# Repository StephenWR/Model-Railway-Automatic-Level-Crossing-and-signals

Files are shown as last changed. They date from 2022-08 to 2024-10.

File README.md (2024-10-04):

# Model-Railway-Automatic-Level-Crossing-and-signals
Arduino based Automatic Level Crossing Gate Controller for double track line on a Model Railway (UK original style gates)
with CMRI reporting to JMRI

This project runs on an Arduino Nano with eight LDR-based sensors distributed along a double-track railway with the old style Level Crossing gates and a station at the centre.  The sensors detect a train entering the section from either side with at least 1 metre of track (n-gauge - more needed for OO or O gauge) to the level crossing gates - this allows time for the gates to close in sequence (exit gates last) to road traffic and open to Train traffic. The sensor for leaving the section is also >1metre away so that long trains will be clear of the gates before opening to road traffic.  Trains entering simultaneously on each track will not trigger the gates to open for road traffic until both have exited the section. Additionally, there is a two-aspect signal at the exit to the station which changes to green when the gates are open for train traffic and changes to red again immediately after being triggered by the train leaving the platform. All the sensor data is sent to a computer running JMRI using a CMRI USB connection - the serial.print lines are commented out when CMRI is running - and are active only when debugging the hardware.

Traffic is only permitted in one direction for each line so that the software is only triggered in the correct sequence—this reduces the chance of spurious triggering and "switch bounce."  Pins are now used for warning signals to road traffic — this is operating now after I designed some for 3D printing using a Resin printer.  Ironically, having spent time designing prototypical hoods for the traffic warning lights, I have had to remove the hoods to make it obvious that the lights are working because they were only viewable at the same height as the road, and most viewers are taller and don't see the lights flashing - i.e. the hoods worked too well!

The version uploaded 3rd October 2024 is used on Maun Valley Junction layout where the station stopping sensors are not used, hence only 6 sensors are used.

3D printing files are available at https://www.thingiverse.com/thing:6786859

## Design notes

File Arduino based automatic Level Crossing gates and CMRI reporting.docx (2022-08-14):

Arduino - based Automatic Level Crossing (on a budget!)

This small project describes an automatic level crossing system controlling 4 UK style Level Crossing Gates, 2 signals (one for the down track and one for the up track) using one “Arduino Nano” (< £9 including terminals) – and 8 LDR sensors in the track (~ 10p each) and 4 small servo motors (<£1 each). The 3D printed parts including the holding base and gates cost <£2.

Our layout has a lower level which is DCC controlled with twin tracks with a station in the middle and a level crossing next to it, and both tracks are fitted with two 3 aspect signals with sensors placed immediately after each signal. The other 2 sensors per track are placed just before and just after the fiddle yards for each circuit – see the simplified schematic below. The outer loop direction is clockwise, the inner loop anticlockwise.

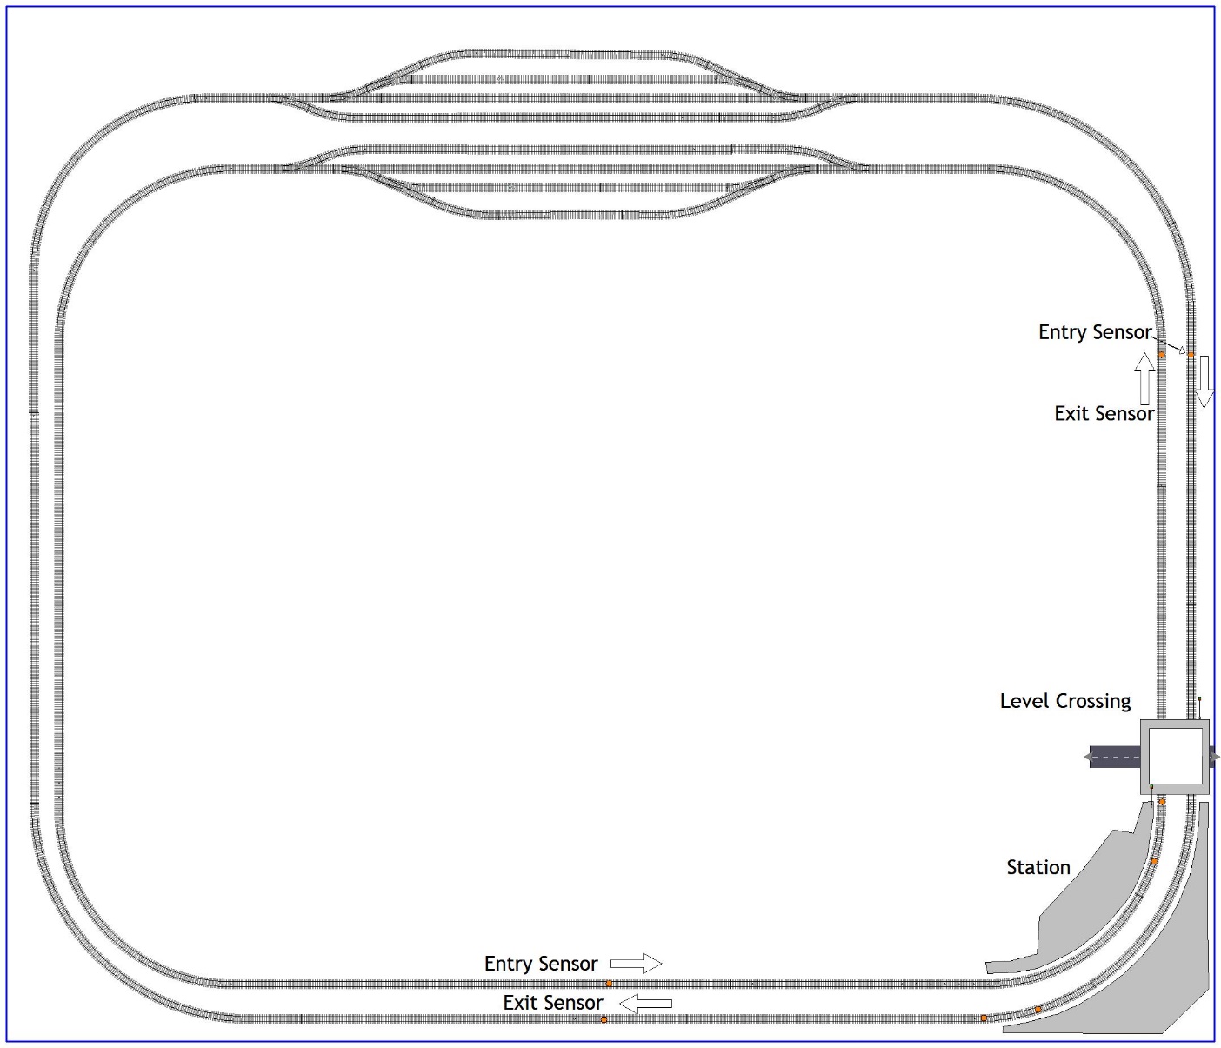
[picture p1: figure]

This project runs on an Arduino Nano with eight LDR based sensors distributed along a double track railway with the old style Level Crossing gates and a station at the centre. The sensors detect a train entering the section from either side with at least 1 metre of track (n-gauge - more needed for OO or O gauge) to the level crossing gates - this allows time for the servo controlled gates to close in sequence (exit gates last) to road traffic and open to Train traffic. The sensor for leaving the section is also >1metre away so that long trains will be clear of the gates before opening to road traffic. Trains entering simultaneously on each track will not trigger the gates to open for road traffic until both have exited the section. Additionally there is a two aspect signal at the exit to the station which changes to green when then the gates are open for train traffic and changes to red again immediately after being triggered by the train leaving the platform. All the sensor data is sent to a computer running JMRI using a CMRI USB connection - the serial.print lines are commented out when CMRI is running - and are active only when debugging the hardware.

Traffic is only permitted in one direction for each line, so that the software is only triggered in the correct sequence - this reduces the chance of spurious triggering and "switch bounce".

The gate mechanism is 3D printed comprising a base which holds 4 servo motors so that the spindles are vertical, a top plate to the base unit to hold in place the spindle extensions into which the Level Crossing Gates engage with a friction fit so that in the case of a train crashing into gates still closed to Trains, little damage will be caused. By default the gates are closed to Trains, and close to traffic in the sequence that moves the left gates first and the right gates last to enable cars on the crossing to exit without hitting the gates.

The Arduino sketch is shown at the GitHub repository under https://github.com/StephenWR/Model-Railway-Automatic-Level-Crossing-and-signals

}

The Arduino Nano with terminal block

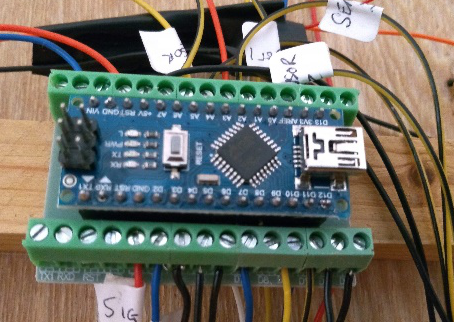
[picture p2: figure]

IR sensor module with 5mm Tx/Rx diodes.

(For n-gauge replace with 3mm diodes)

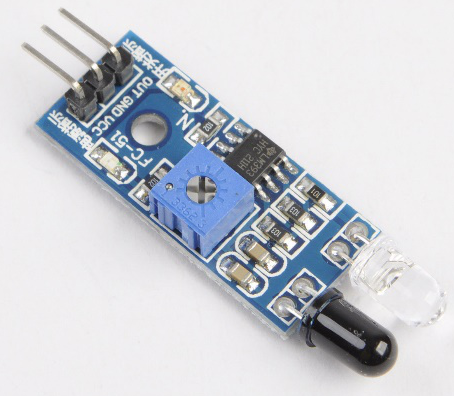
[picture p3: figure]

MERG Arduino Workshop 26Oct19.docx © Stephen Wadsworth 2019Page 1 of 3

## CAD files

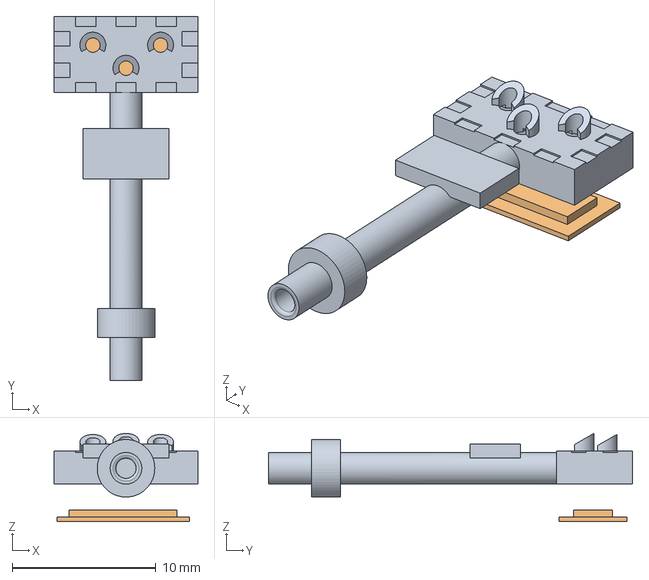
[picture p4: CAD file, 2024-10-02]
Level crossing warning lights 6.FCStd
10.0 x 25.3 x 6.12 mm

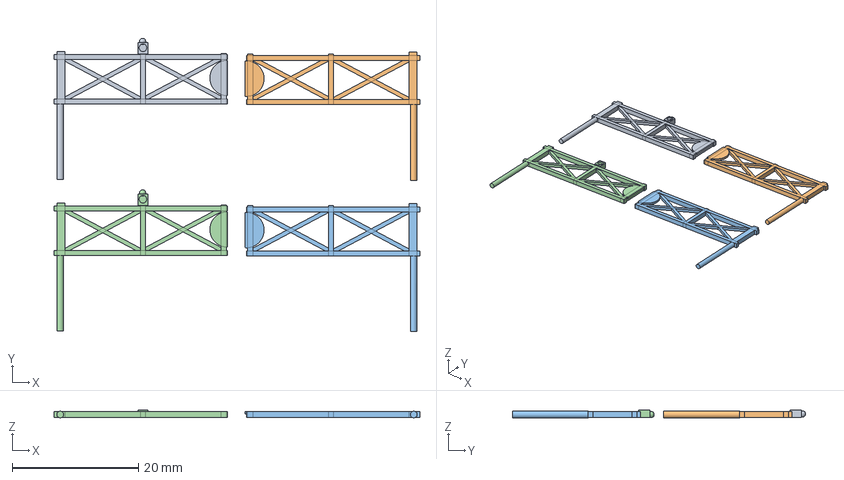
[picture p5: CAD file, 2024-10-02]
Level crossing gates v2 n gauge.FCStd
58.0 x 46.5 x 1.23 mm

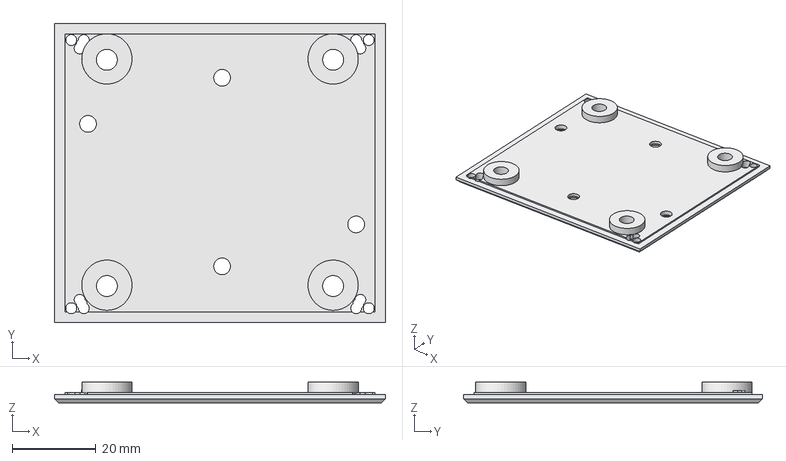
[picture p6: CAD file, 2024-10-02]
Level crossing top6 n gauge.FCStd
79.0 x 71.5 x 5.00 mm

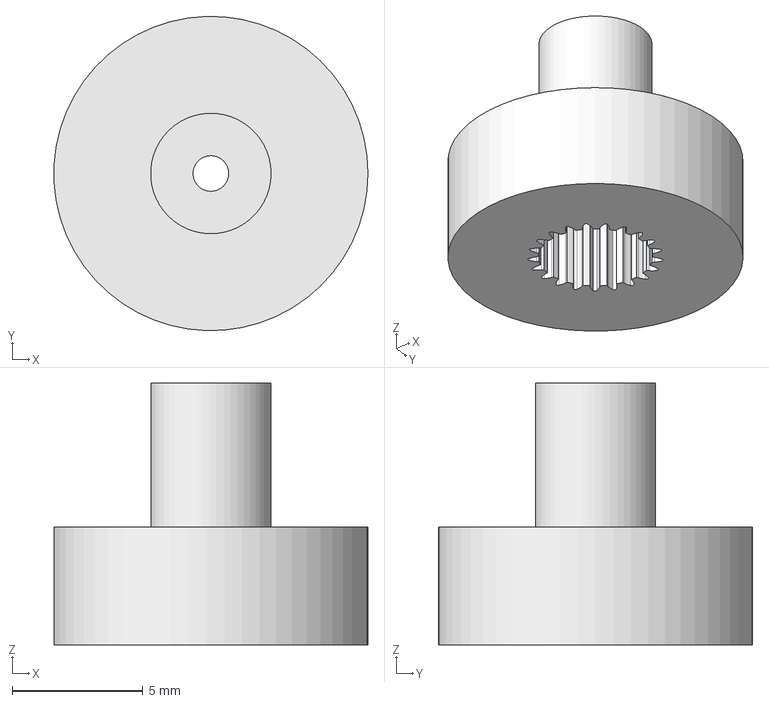
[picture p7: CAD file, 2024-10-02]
LC Servo top 21x0235intgear short5mm.FCStd
12.0 x 12.0 x 10.0 mm

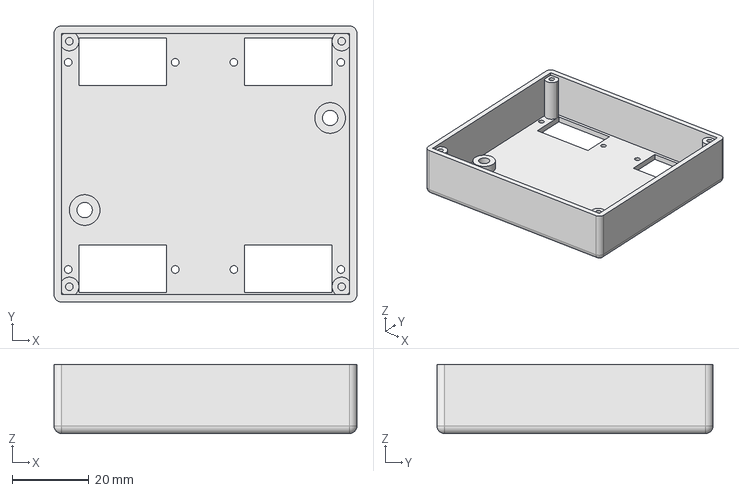
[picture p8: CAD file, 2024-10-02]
Level crossing base5 n gauge.FCStd
79.0 x 72.0 x 18.0 mm

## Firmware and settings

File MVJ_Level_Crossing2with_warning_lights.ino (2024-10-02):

#include <CMRI.h>
// CMRI Settings
#define CMRI_ADDR 2 //CMRI node address in JMRI

// Define CMRI connection with 24 inputs and 24 outputs
CMRI cmri(CMRI_ADDR, 24, 24);

#include <VarSpeedServo.h>  //servo library that enables servo speed control and operation without delaying the main loop
#define numSensitivity 600  //difference that 2 readings of the LDR sensors between covered and uncovered

// create servo object to control a servo
VarSpeedServo myservo1;
VarSpeedServo myservo2;
VarSpeedServo myservo3;
VarSpeedServo myservo4;

// create constants to read Light Dependant Resistor measurement by analogue ports

int const ldrPin1 = A0; // analog pin used to connect to LDR sensor1
int const ldrPin2 = A1; // analog pin used to connect to LDR sensor2
int const ldrPin3 = A2; // analog pin used to connect to LDR sensor3
int const ldrPin4 = A3; // analog pin used to connect to LDR sensor4
int const ldrPin5 = A4; // analog pin used to connect to LDR sensor5
int const ldrPin6 = A5; // analog pin used to connect to LDR sensor6
//int const ldrPin7 = A6; // analog pin used to connect to LDR sensor7
//int const ldrPin8 = A7; // analog pin used to connect to LDR sensor8

int RED1 = 2;
int GREEN1 = 4;
int RED2 = 8;
int GREEN2 = 10;
int POWER = 12;
int ORANGE = 11;
int WARNLEFT = 13;
int WARNRIGHT = 7;

// Variables

unsigned long previousMillis1 = 0;  // timing between start of level crossing sequence and gates closing - inner loop
unsigned long previousMillis2 = 0;  // timing between start of level crossing sequence and gates closing - outer loop
unsigned long previousMillis3 = 0;  // used in initial tests for start of level crossing sequence - now using sensors
unsigned long previousMillis4 = 0;  // flashing of red warning lights
unsigned long previousMillis5 = 0;  // orange to red lights

unsigned long currentMillis;// = millis();   // used for lights start / stop sequence

long interval = 3500;  // interval at which to change signal lights and half interval to close 2nd gates to traffic


int ldrVal1;  // variable to read the value from the analog pin A0
int ldrVal2;  // variable to read the value from the analog pin A1
int ldrVal3;  // variable to read the value from the analog pin A2
int ldrVal4;  // variable to read the value from the analog pin A3
int ldrVal5;  // variable to read the value from the analog pin A4
int ldrVal6;  // variable to read the value from the analog pin A5
//int ldrVal7;  // variable to read the value from the analog pin A6
//int ldrVal8;  // variable to read the value from the analog pin A7

int ldrVal1a;  // variable to read the value from the analog pin A0
int ldrVal2a;  // variable to read the value from the analog pin A1
int ldrVal3a;  // variable to read the value from the analog pin A2
int ldrVal4a;  // variable to read the value from the analog pin A3
int ldrVal5a;  // variable to read the value from the analog pin A4
int ldrVal6a;  // variable to read the value from the analog pin A5
//int ldrVal7a;  // variable to read the value from the analog pin A6
//int ldrVal8a;  // variable to read the value from the analog pin A7

int ldrVal1i;  // variable to store the initial value from the analog pin A0
int ldrVal2i;  // variable to store the initial value from the analog pin A1
int ldrVal3i;  // variable to store the initial value from the analog pin A2
int ldrVal4i;  // variable to store the initial value from the analog pin A3
int ldrVal5i;  // variable to store the initial vaule from the analog pin A4
int ldrVal6i;  // variable to store the initial value from the analog pin A5
int ldrVal1i1;  // variable to store the second initial value from the analog pin A0
int ldrVal2i1;  // variable to store the second initial value from the analog pin A1
int ldrVal3i1;  // variable to store the second initial value from the analog pin A2
int ldrVal4i1;  // variable to store the second initial value from the analog pin A3
int ldrVal5i1;  // variable to store the second initial vaule from the analog pin A4
int ldrVal6i1;  // variable to store the second initial value from the analog pin A5
//int ldrVal7i;  // variable to store the second initial vaule from the analog pin A6
//int ldrVal8i;  // variable to store the second initial value from the analog pin A7

bool lineinnerclear;
bool lineouterclear;
bool outer2;
bool outer3;
bool outer4;
//bool outerstop;
bool inner4;
bool inner5;
bool inner6;
//bool innerstop;
bool warnlights;
bool orangewarn;
bool redwarn;
bool redwarn2;

int LEF = 145;
int RIG = 45;

int SPEED1 = 25;
int SPEED2 = 25;

void setup() {

  // initialize serial port:
  // Start the serial connection to JMRI computer
  Serial.begin(19200);  //Baud rate of 19200 usually used, so ensure this matches the baud rate in JMRI,
  // using a faster rate can make processing faster but can also result in incomplete data

  pinMode(RED1, OUTPUT);
  pinMode(RED2, OUTPUT);
  pinMode(GREEN1, OUTPUT);
  pinMode(GREEN2, OUTPUT);
  pinMode(POWER, OUTPUT);
  pinMode(ORANGE, OUTPUT);
  pinMode(WARNLEFT, OUTPUT);
  pinMode(WARNRIGHT, OUTPUT);

  digitalWrite(POWER, HIGH);
  digitalWrite(GREEN1, HIGH);
  digitalWrite(RED1, LOW);
  digitalWrite(GREEN2, HIGH);
  digitalWrite(RED2, LOW);
  digitalWrite(ORANGE, HIGH);
  digitalWrite(WARNLEFT, HIGH);
  digitalWrite(WARNRIGHT, HIGH);
  // initialise servo ports:
  myservo1.attach(3);  // connect servo 1 to pin 3
  myservo2.attach(5);  // connect servo 2 to pin 5
  myservo3.attach(6);  // connect servo 3 to pin 6
  myservo4.attach(9);  // connect servo 4 to pin 9

  // take initial readings for LDR's
  ldrVal1i = analogRead(ldrPin1); // read the value of LDR Sensor 1
  ldrVal2i = analogRead(ldrPin2); // read the value of LDR Sensor 2
  ldrVal3i = analogRead(ldrPin3); // read the value of LDR Sensor 3
  ldrVal4i = analogRead(ldrPin4); // read the value of LDR Sensor 4
  ldrVal5i = analogRead(ldrPin5); // read the value of LDR Sensor 5
  ldrVal6i = analogRead(ldrPin6); // read the value of LDR Sensor 6
  // and again
  ldrVal1i1 = analogRead(ldrPin1); // read the value of LDR Sensor 1
  ldrVal2i1 = analogRead(ldrPin2); // read the value of LDR Sensor 2
  ldrVal3i1 = analogRead(ldrPin3); // read the value of LDR Sensor 3
  ldrVal4i1 = analogRead(ldrPin4); // read the value of LDR Sensor 4
  ldrVal5i1 = analogRead(ldrPin5); // read the value of LDR Sensor 5
  ldrVal6i1 = analogRead(ldrPin6); // read the value of LDR Sensor 6
  //  ldrVal7i = analogRead(ldrPin7); // read the value of LDR Sensor 7
  //  ldrVal8i = analogRead(ldrPin8); // read the value of LDR Sensor 8
  // Add the 2 readings together
  ldrVal1i = ldrVal1i + ldrVal1i1;
  ldrVal2i = ldrVal2i + ldrVal2i1;
  ldrVal3i = ldrVal3i + ldrVal3i1;
  ldrVal4i = ldrVal4i + ldrVal4i1;
  ldrVal5i = ldrVal5i + ldrVal5i1;
  ldrVal6i = ldrVal6i + ldrVal6i1;
  // Printout the initial values for debugging only
  //  Serial.print(" 6: ");
  //  Serial.print(ldrVal6i);
  //  Serial.print("  5: ");
  //  Serial.print(ldrVal5i);
  //  Serial.print(" 4: ");
  //  Serial.print(ldrVal4i);
  //  Serial.print("  3: ");
  //  Serial.print(ldrVal3i);
  //  Serial.print("  2: ");
  //  Serial.print(ldrVal2i);
  //  Serial.print("  1: ");
  //  Serial.print(ldrVal1i);

  outer2 = false;
  outer3 = false;
  outer4 = false;
  //  outerstop = false;
  inner4 = false;
  inner5 = false;
  inner6 = false;
  //  innerstop = false;
  warnlights = false;
  orangewarn = false;
  redwarn = false;
  redwarn2 = false;


  myservo1.write(LEF, SPEED1);
  myservo2.write(RIG, SPEED2);
  myservo3.write(LEF, SPEED2);
  myservo4.write(RIG, SPEED2);
  myservo1.wait();  // This only ok to use in setup section as is blocking code
  myservo2.wait();

  lineinnerclear = true;
  lineouterclear = true;

  cmri.set_bit(0, outer2);  //Bit 0 = address 2001 in JMRI as this is set to CMRI Node 2
  cmri.set_bit(1, outer3);
  cmri.set_bit(2, outer4);
  // cmri.set_bit(3, outerstop);
  cmri.set_bit(4, inner4);
  cmri.set_bit(5, inner5);
  cmri.set_bit(6, inner6);
  //  cmri.set_bit(7, innerstop);
  cmri.process();
}

// Setup states for inner and outerlines

enum LINESTATEinner
{
  inner_ENTER,
  //  inner_STOP,
  inner_SIGNAL,
  inner_EXIT,
};
enum LINESTATEouter
{
  outer_ENTER,
  //  outer_STOP,
  outer_SIGNAL,
  outer_EXIT,
};
//  Initial states for inner and outer lines

LINESTATEinner lineinnerState = inner_ENTER;
LINESTATEouter lineouterState = outer_ENTER;

// Main Loop

void loop() {
  currentMillis = millis();
  cmri.process();   // only process when something changes

  int LEF = 145;
  int RIG = 45;

  int SPEED1 = 15;
  int SPEED2 = 15;
  ldrVal1 = analogRead(ldrPin1); // read the value of LDR Sensor 1
  ldrVal2 = analogRead(ldrPin2); // read the value of LDR Sensor 2
  ldrVal3 = analogRead(ldrPin3); // read the value of LDR Sensor 3
  ldrVal4 = analogRead(ldrPin4); // read the value of LDR Sensor 4
  ldrVal5 = analogRead(ldrPin5); // read the value of LDR Sensor 5
  ldrVal6 = analogRead(ldrPin6); // read the value of LDR Sensor 6
  //  ldrVal7 = analogRead(ldrPin7); // read the value of LDR Sensor 7
  //  ldrVal8 = analogRead(ldrPin8); // read the value of LDR Sensor 8

  ldrVal1a = analogRead(ldrPin1); // read the value of LDR Sensor 1
  ldrVal2a = analogRead(ldrPin2); // read the value of LDR Sensor 2
  ldrVal3a = analogRead(ldrPin3); // read the value of LDR Sensor 3
  ldrVal4a = analogRead(ldrPin4); // read the value of LDR Sensor 4
  ldrVal5a = analogRead(ldrPin5); // read the value of LDR Sensor 5
  ldrVal6a = analogRead(ldrPin6); // read the value of LDR Sensor 6
  //  ldrVal7a = analogRead(ldrPin7); // read the value of LDR Sensor 7
  //  ldrVal8a = analogRead(ldrPin8); // read the value of LDR Sensor 8

  ldrVal1 = ldrVal1 + ldrVal1a;
  ldrVal2 = ldrVal2 + ldrVal2a;
  ldrVal3 = ldrVal3 + ldrVal3a;
  ldrVal4 = ldrVal4 + ldrVal4a;
  ldrVal5 = ldrVal5 + ldrVal5a;
  ldrVal6 = ldrVal6 + ldrVal6a;
  //  ldrVal7 = ldrVal7 + ldrVal7a;
  //  ldrVal8 = ldrVal8 + ldrVal8a;


  cmri.set_bit(0, outer2);  //Bit 0 = address 2001 in JMRI
  cmri.set_bit(1, outer3);
  cmri.set_bit(2, outer4);
  //  cmri.set_bit(3, outerstop);
  cmri.set_bit(4, inner4);
  cmri.set_bit(5, inner5);
  cmri.set_bit(6, inner6);
  //  cmri.set_bit(7, innerstop);
  cmri.process();


  //  print out the value to the Serial Monitor whilst debugging only
  //    Serial.print("ldrVal8: ");
  //    Serial.print(ldrVal8);
  //    Serial.print("   ldrVal7: ");
  //    Serial.print(ldrVal7);
  //    Serial.print(" 6: ");
  //    Serial.print(ldrVal6);
  //    Serial.print("  5: ");
  //    Serial.print(ldrVal5);
  //    Serial.print(" 4: ");
  //    Serial.print(ldrVal4);
  //    Serial.print("  3: ");
  //    Serial.print(ldrVal3);
  //    Serial.print("  2: ");
  //    Serial.print(ldrVal2);
  //    Serial.print("  1: ");
  //    Serial.print(ldrVal1);
  //    Serial.print("  inline: ");
  //    Serial.print(lineinnerState);
  //    Serial.print("  ");
  //    Serial.print(lineinnerclear);
  //    Serial.print("  outline: ");
  //    Serial.print(lineouterState);
  //    Serial.print("  ");
  //    Serial.println(lineouterclear);
  //delay(50);

  switch (lineinnerState)  // inner track
  {
    case inner_ENTER:
      lineinnerenter(ldrVal1, ldrVal2, ldrVal3);
      break;
    //    case inner_STOP:
    //      lineinnerstop(ldrVal1, ldrVal2, ldrVal3);
    //      break;
    case inner_SIGNAL:
      lineinnersignal(ldrVal1, ldrVal2, ldrVal3);
      break;
    case inner_EXIT:
      lineinnerexit(ldrVal1, ldrVal2, ldrVal3);
      break;
  }
  switch (lineouterState)  // outer track
  {
    case outer_ENTER:
      lineouterenter(ldrVal4, ldrVal5, ldrVal6);
      break;
    //    case outer_STOP:
    //      lineouterstop(ldrVal4, ldrVal5, ldrVal6);
    //      break;
    case outer_SIGNAL:
      lineoutersignal(ldrVal4, ldrVal5, ldrVal6);
      break;
    case outer_EXIT:
      lineouterexit(ldrVal4, ldrVal5, ldrVal6);
      break;
  }

  if (redwarn and ((currentMillis - previousMillis4) > 400)) {
    digitalWrite(WARNLEFT, HIGH);
    digitalWrite(WARNRIGHT, LOW);
    redwarn = false;
    redwarn2 = true;
    previousMillis4 = currentMillis;
  }
  if (redwarn2 and ((currentMillis - previousMillis4) > 400)) {
    digitalWrite(WARNLEFT, LOW);
    digitalWrite(WARNRIGHT, HIGH);
    redwarn2 = false;
    redwarn = true;
    previousMillis4 = currentMillis;
  }
}
// End of main loop

// What to do with the results for inner and outer lines -------------------------------------------

void lineinnerexit(int ldrVal1, int ldrVal2, int ldrVal3) {
  if (ldrVal3 > (ldrVal3i + numSensitivity)) {
    lineinnerclear = true;
    inner6 = true;
    inner5 = false;
    cmri.set_bit(5, inner5);
    cmri.set_bit(6, inner6);

    if (lineinnerclear and lineouterclear) {
      Serial.println(" open gates to traffic ");
      myservo1.write(LEF, SPEED1);
      myservo2.write(RIG, SPEED2);
      myservo3.write(LEF, SPEED2);
      myservo4.write(RIG, SPEED2);
      warnlights = false;
      redwarn = false;
      redwarn2 = false;
      digitalWrite(WARNLEFT, HIGH);
      digitalWrite(WARNRIGHT, HIGH);
      digitalWrite(ORANGE, HIGH);
      previousMillis5 = currentMillis;
    }
    lineinnerState = inner_ENTER;
  }
}

void lineinnerenter(int ldrVal1, int ldrVal2, int ldrVal3) {
  if (ldrVal1 > (ldrVal1i + numSensitivity)) {
    Serial.println(" closing gates to traffic ");
    lineinnerclear = false;
    inner4 = true;
    inner6 = false;
    cmri.set_bit(4, inner4);
    cmri.set_bit(6, inner6);

    if (!warnlights) {  //Start of crossing warning light sequence
      previousMillis5 = currentMillis;
      digitalWrite(ORANGE, LOW);
      orangewarn = true;
      warnlights = true;
    }
    lineinnerState = inner_SIGNAL;
    previousMillis1 = millis();
  }
}

//void lineinnerstop(int ldrVal1, int ldrVal2, int ldrVal3) {
//  unsigned long currentMillis1 = millis();
//  if (currentMillis1 - previousMillis1 > (interval / 2)) {
//    myservo2.write(LEF, SPEED1);
//    myservo4.write(LEF, SPEED2);
//  }
//  if (currentMillis1 - previousMillis1 > interval) {
//    previousMillis1 = currentMillis1;
//    digitalWrite(GREEN1, LOW);
//    digitalWrite(RED1, HIGH); // turn signal from red to green
//  }
//  if (ldrVal8 > (ldrVal8i + numSensitivity)) {  // should be ldrVal8
//
//    inner4 = false;
//    innerstop = true;
//    cmri.set_bit(4, inner4);
//    cmri.set_bit(7, innerstop);
//
//    lineinnerState = inner_SIGNAL;
//    previousMillis1 = millis();
//  }
//}

void lineinnersignal(int ldrVal1, int ldrVal2, int ldrVal3) {
  unsigned long currentMillis1 = millis();
  if (orangewarn and ((currentMillis - previousMillis5) > 1500)) {
    redwarn = true;
    orangewarn = false;
    digitalWrite(WARNLEFT, LOW);
    digitalWrite(WARNRIGHT, LOW);
    digitalWrite(ORANGE, HIGH);
    previousMillis4 = currentMillis;
  }
  if (redwarn and ((currentMillis - previousMillis5) > 3000)) {
    myservo1.write(RIG, SPEED1);
    myservo3.write(RIG, SPEED2);
  }

  if (currentMillis - previousMillis1 > ((interval / 2) + 3000)) { // start other gates moving
    myservo2.write(LEF, SPEED1);
    myservo4.write(LEF, SPEED2);
  }

  if (ldrVal2 > (ldrVal2i + numSensitivity)) {
    lineinnerState = inner_EXIT;
    inner5 = true;
    //    innerstop = false;
    cmri.set_bit(5, inner5);
    //   cmri.set_bit(7, innerstop);
    digitalWrite(GREEN1, HIGH);
    digitalWrite(RED1, LOW); // turn signal red
  }
}

// outer line commands ------------------------------------------------------------------------------------
void lineouterexit(int ldrVal4, int ldrVal5, int ldrVal6) {
  if (ldrVal6 > (ldrVal6i + numSensitivity)) {
    lineouterclear = true;
    outer4 = true;
    outer3 = false;
    cmri.set_bit(2, outer4);
    cmri.set_bit(1, outer3);

    if (lineinnerclear and lineouterclear) {
      Serial.println(" open gates to traffic ");
      myservo1.write(LEF, SPEED1);
      myservo2.write(RIG, SPEED2);
      myservo3.write(LEF, SPEED2);
      myservo4.write(RIG, SPEED2);
      warnlights = false;
      redwarn = false;
      redwarn2 = false;
      digitalWrite(WARNLEFT, HIGH);
      digitalWrite(WARNRIGHT, HIGH);
      digitalWrite(ORANGE, HIGH);
      previousMillis5 = currentMillis;
    }
    lineouterState = outer_ENTER;
  }
}
void lineouterenter(int ldrVal4, int ldrVal5, int ldrVal6) {
  if (ldrVal4 > (ldrVal4i + numSensitivity)) {
    Serial.println(" closing gates to traffic ");
    lineouterclear = false;
    outer4 = false;
    outer2 = true;
    cmri.set_bit(0, outer2);  //Bit 0 = address 2001 in JMRI
    cmri.set_bit(2, outer4);

    if (!warnlights) {  //Start of crossing warning light sequence
      previousMillis5 = currentMillis;
      digitalWrite(ORANGE, LOW);
      orangewarn = true;
      warnlights = true;
    }

    lineouterState = outer_SIGNAL;
    previousMillis2 = millis();
  }
}

//void lineouterstop(int ldrVal4, int ldrVal5, int ldrVal6) {
//  unsigned long currentMillis2 = millis();
//  if (currentMillis2 - previousMillis2 > (interval / 2)) { // start other gates moving
//    myservo2.write(LEF, SPEED1);
//    myservo4.write(LEF, SPEED2);
//  }
//  if (currentMillis2 - previousMillis2 > interval) {
//    previousMillis2 = currentMillis2;
//    digitalWrite(GREEN2, LOW);
//    digitalWrite(RED2, HIGH); // turn signal from red to green
//  }
//
//  if (ldrVal7 > (ldrVal7i + numSensitivity)) {
//    lineouterState = outer_SIGNAL;
//    outerstop = true;
//    outer2 = false;
//    cmri.set_bit(3, outerstop);
//    cmri.set_bit(0, outer2);
//  }
//}

void lineoutersignal(int ldrVal4, int ldrVal5, int ldrVal6) {
  unsigned long currentMillis2 = millis();
  if (orangewarn and ((currentMillis - previousMillis5) > 1500)) {
    redwarn = true;
    orangewarn = false;
    digitalWrite(WARNLEFT, LOW);
    digitalWrite(WARNRIGHT, LOW);
    digitalWrite(ORANGE, HIGH);
    previousMillis4 = currentMillis;
  }
  if (redwarn and ((currentMillis - previousMillis5) > 3000)) {
    myservo1.write(RIG, SPEED1);
    myservo3.write(RIG, SPEED2);
  }

  if (currentMillis - previousMillis2 > ((interval / 2) + 3000)) { // start other gates moving
    myservo2.write(LEF, SPEED1);
    myservo4.write(LEF, SPEED2);
  }
  if (ldrVal5 > (ldrVal5i + numSensitivity)) {
    lineouterState = outer_EXIT;
    outer3 = true;
    //    outerstop = false;
    //    cmri.set_bit(3, outerstop);
    cmri.set_bit(1, outer3);

    digitalWrite(GREEN2, HIGH);
    digitalWrite(RED2, LOW); // turn signal red
  }
}

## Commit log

2022-08-13 Add files via upload
    This version now uses millis instaed of waiting for the first two gates to finish closing, so that a train entering from the opposite direction does not get missed, and the gates will not close at an unwanted time. The LDR detectors are also read twice and averaged to prevent spurious triggering due to electrical noise - mainly the DCC bus / track near the sensors.
    [LC4Servo1k.ino]
2024-10-02 Add files via upload
    These FreeCad files show the designs for the physical servo holder and top, the gate holders which sit on top of SG90 servos (4 required), and the gates, which are like square pegs in a round hole which allows them to slip if obstructions are in the way of the gates opening or closing.
    [LC Servo top 21x0235intgear short5mm.FCStd, Level crossing base5 n gauge.FCStd, Level crossing gates v2 n gauge.FCStd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]
